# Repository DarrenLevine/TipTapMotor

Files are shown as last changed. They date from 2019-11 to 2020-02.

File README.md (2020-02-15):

# TipTapMotor

## Print one of each STL, except for:
* "GearBoxAssy-Planet.STL", which needs a total of three.
* "SingleMotorPCBspacer.STL", which is optional, but needs a total of two.
Note: I used the LulzbotMini_TipTap.curaprofile on my lulzbot mini to get the tight tolerances needed on the gears and good first layer resolution.

## Purchased Parts:
* Qty 1. DirectServo pcb: https://github.com/DarrenLevine/DirectServo/tree/master/Manufacturing
* Qty 3. 18-8 Stainless Steel Dowel Pin, 1mm Diameter, 12mm Length (hammered into the three holes of the "GearboxFace-LowerInner.STL")
* Qty 15. 96817A156 Thread Forming Screw for Thin Plastic
* Qty 1. iPower GBM3506H-130T Gimbal Brushless Motor
* Qty 4. M3x10mm Nylon bolt and nut (for PCB mounting)
* Qty 2. M3x6mm Nylon bolt and nut (for motor mounting)
* Qty 1. 6705 Thin Section Metric Ball Bearing Open 25x32x4
* Qty 3. 623ZZ 3mm x 10mm x 4mm Shielded Deep Groove Precision Ball Bearings
* Qty 3. Flat Head Screws M3 x 0.5 mm Thread, 6 mm Long (91420A116)
* Qty 1. Small diametric encoder magnet such as: https://www.kjmagnetics.com/proddetail.asp?prod=d82dia

## Assembly according to cross section:
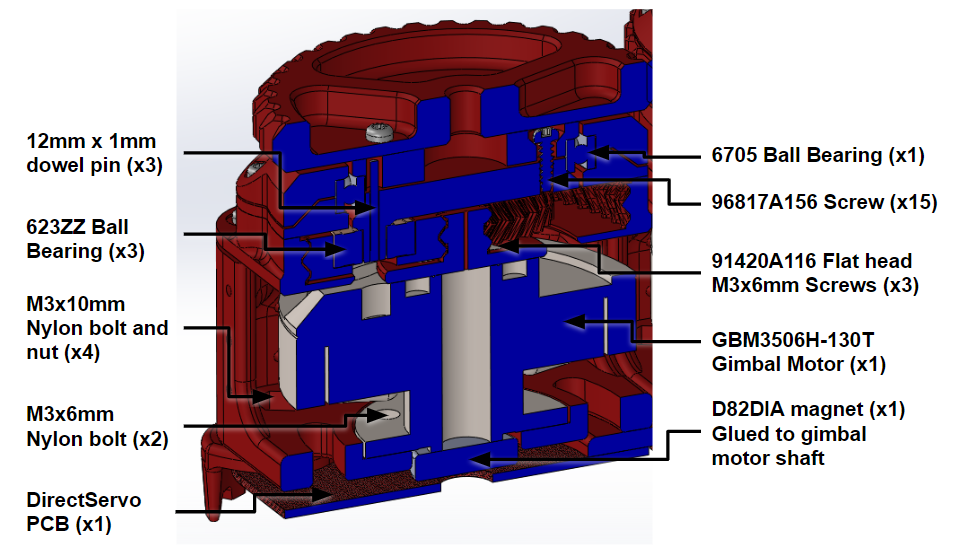
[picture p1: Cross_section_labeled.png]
Cross_section_labeled


## Final product:
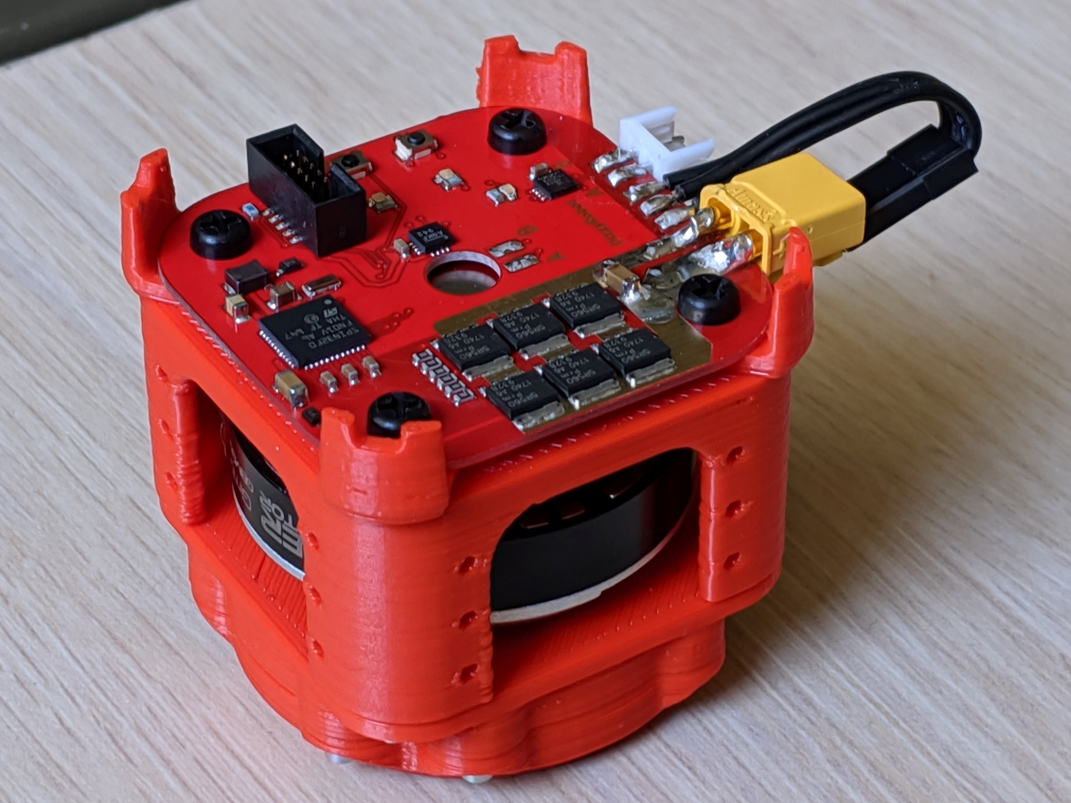
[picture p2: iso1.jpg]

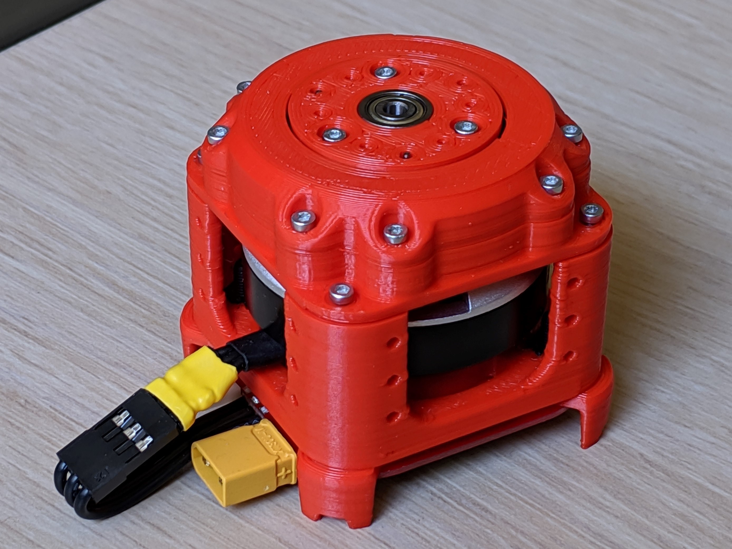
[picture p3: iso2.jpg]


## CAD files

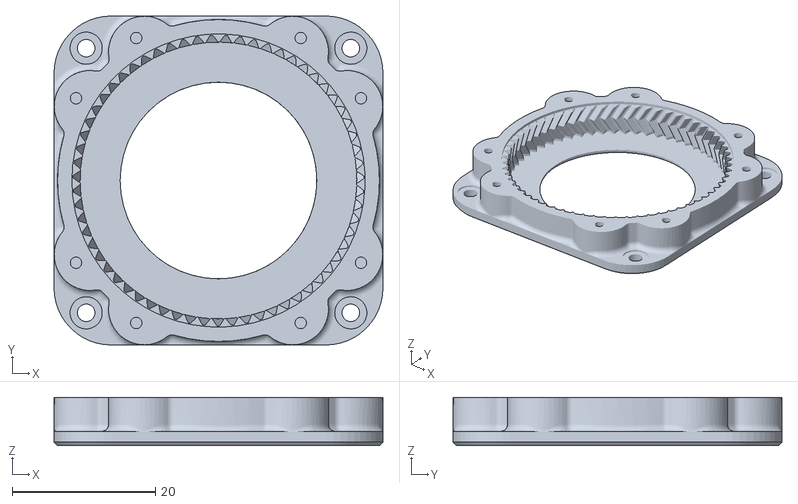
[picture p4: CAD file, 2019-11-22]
GearBoxAssy-Ring.STL
46.0 x 46.0 x 6.75

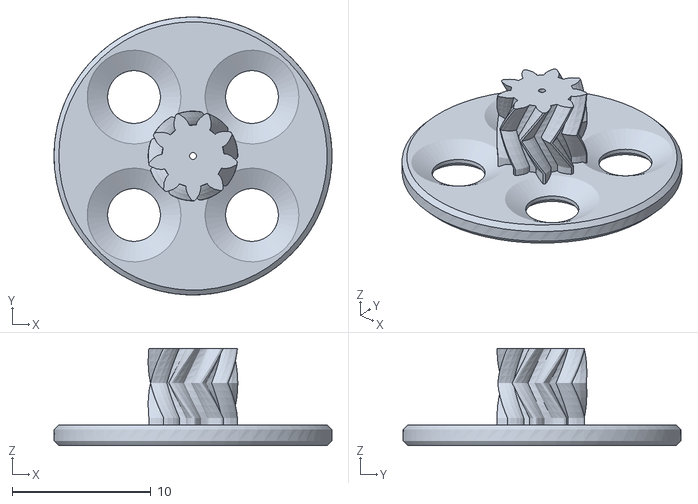
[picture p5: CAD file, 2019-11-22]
GearBoxAssy-Sun.STL
20.0 x 20.0 x 7.00

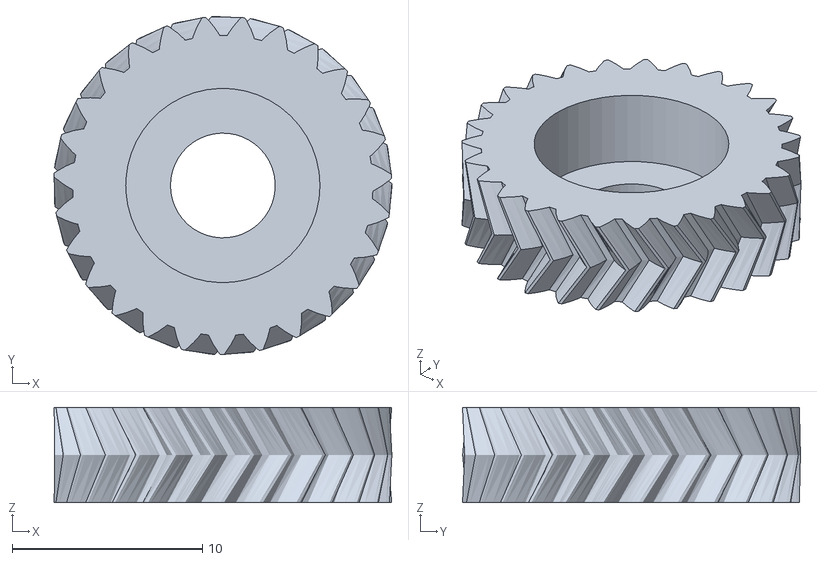
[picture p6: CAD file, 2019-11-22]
GearBoxAssy-Planet.STL
17.7 x 17.7 x 5.00

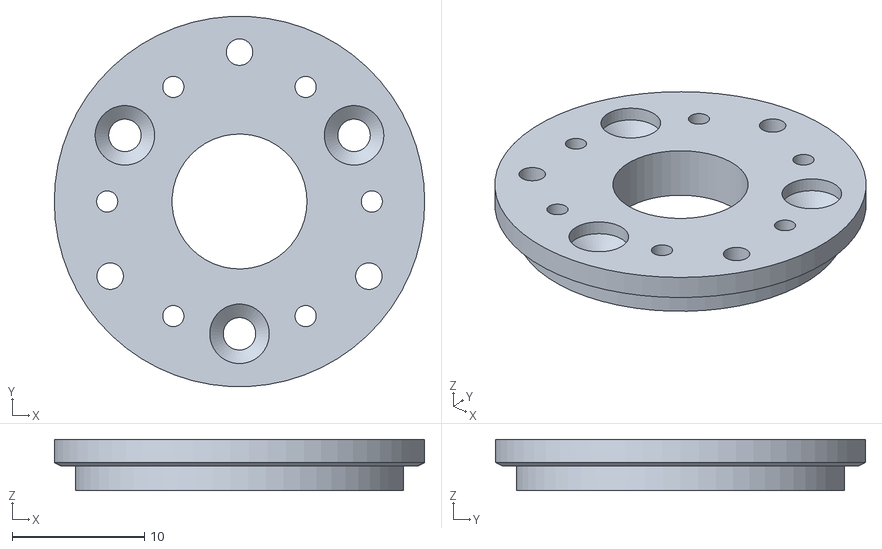
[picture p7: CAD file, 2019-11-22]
GearboxFace-UpperInner.STL
28.0 x 28.0 x 3.88

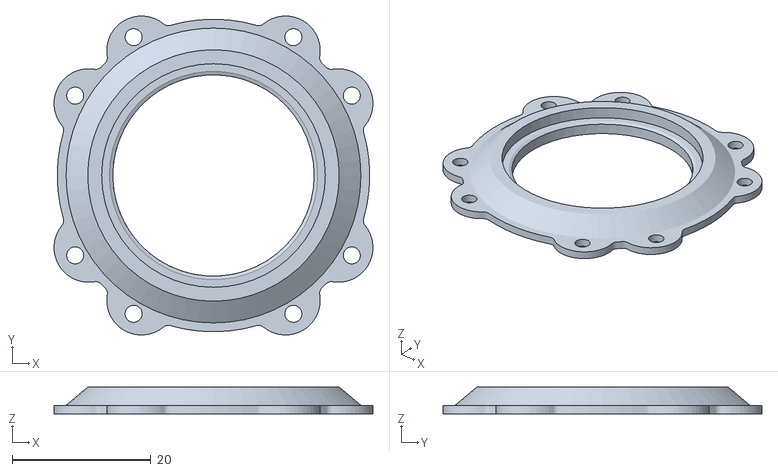
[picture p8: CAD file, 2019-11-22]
GearboxFace-LowerOuter.STL
45.9 x 45.9 x 3.88

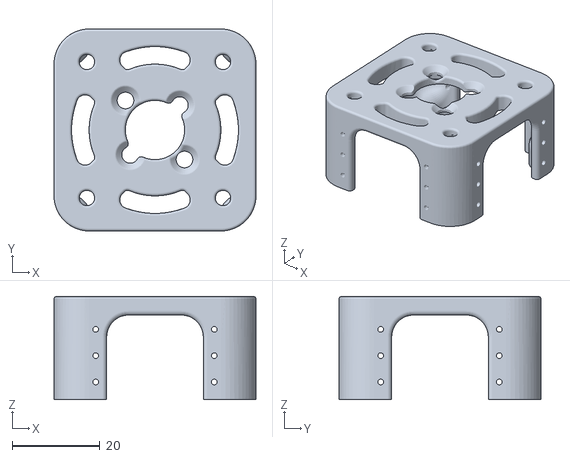
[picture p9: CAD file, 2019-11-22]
Motor_Case.STL
46.0 x 46.0 x 23.5

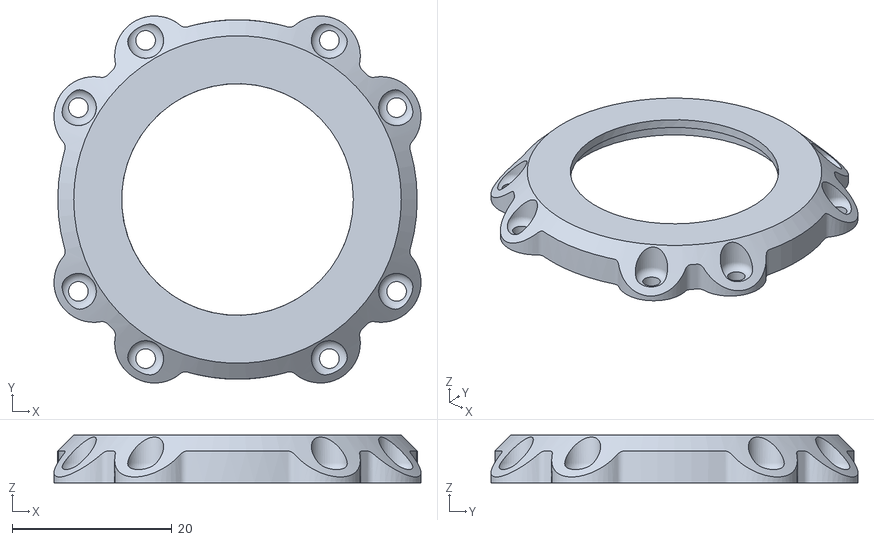
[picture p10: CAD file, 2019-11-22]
GearboxFace-UpperOuter.STL
45.9 x 45.9 x 6.00

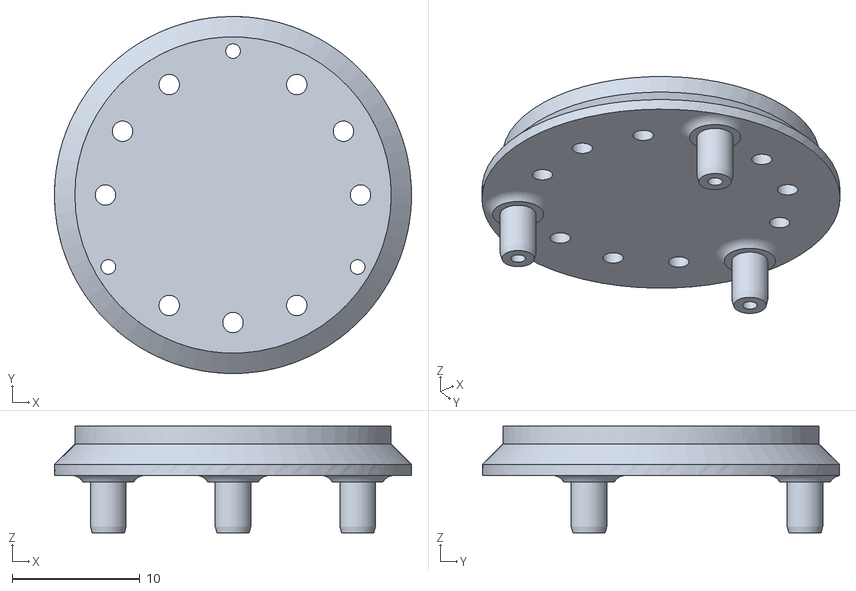
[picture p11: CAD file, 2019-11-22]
GearboxFace-LowerInner.STL
28.0 x 28.0 x 8.38

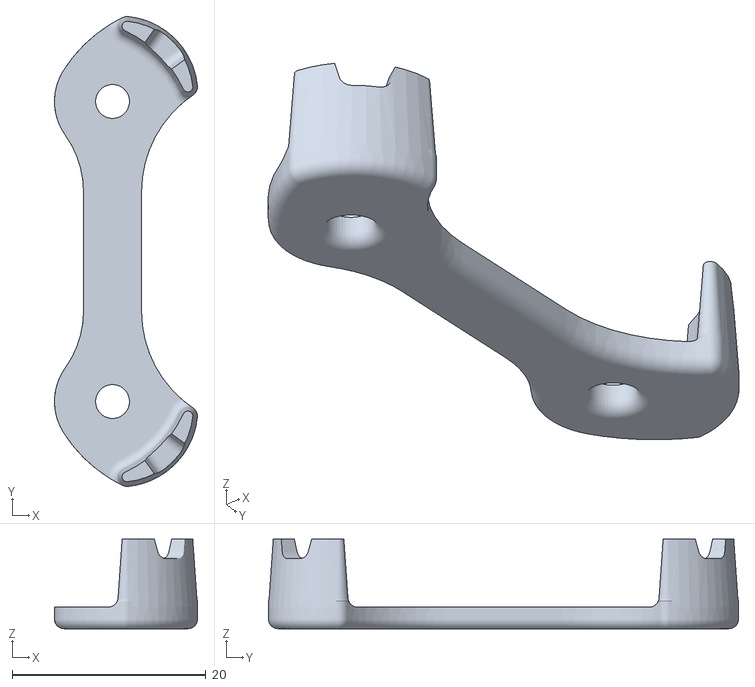
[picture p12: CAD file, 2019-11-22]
SingleMotorPCBspacer.STL
14.8 x 48.6 x 9.25
